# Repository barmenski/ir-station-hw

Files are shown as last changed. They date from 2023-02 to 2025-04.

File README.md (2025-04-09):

# Overview

IR rework station is made up of halogen lamp 250 mm for bottom heater, ceramic heater 450 Watts for top. Raspberry Pi B+ v1.2 controls the process.

## How to use

1. Install Raspbian on ypur Raspberry Pi https://www.raspberrypi.com/documentation/computers/getting-started.html#installing-the-operating-system
2. Install Node.js:
   1. Install NVM with the install script:
      `curl -o- https://raw.githubusercontent.com/nvm-sh/nvm/v0.40.1/install.sh | bash`
   2. Install the latest Long Term Support version of Node with NVM:
      `nvm install --lts`
3. Install Git:
   `sudo apt install git -y`
4. Clone repository:
   `git clone https://github.com/barmenski/ir-station-hw.git`
5. Go to ir-station-hw directory:
   `cd ./ir-station-hw/`
6. Install dependencies:
   `npm install`
7. Run:
   `node index.js`

## Peripheral devices connection diagram

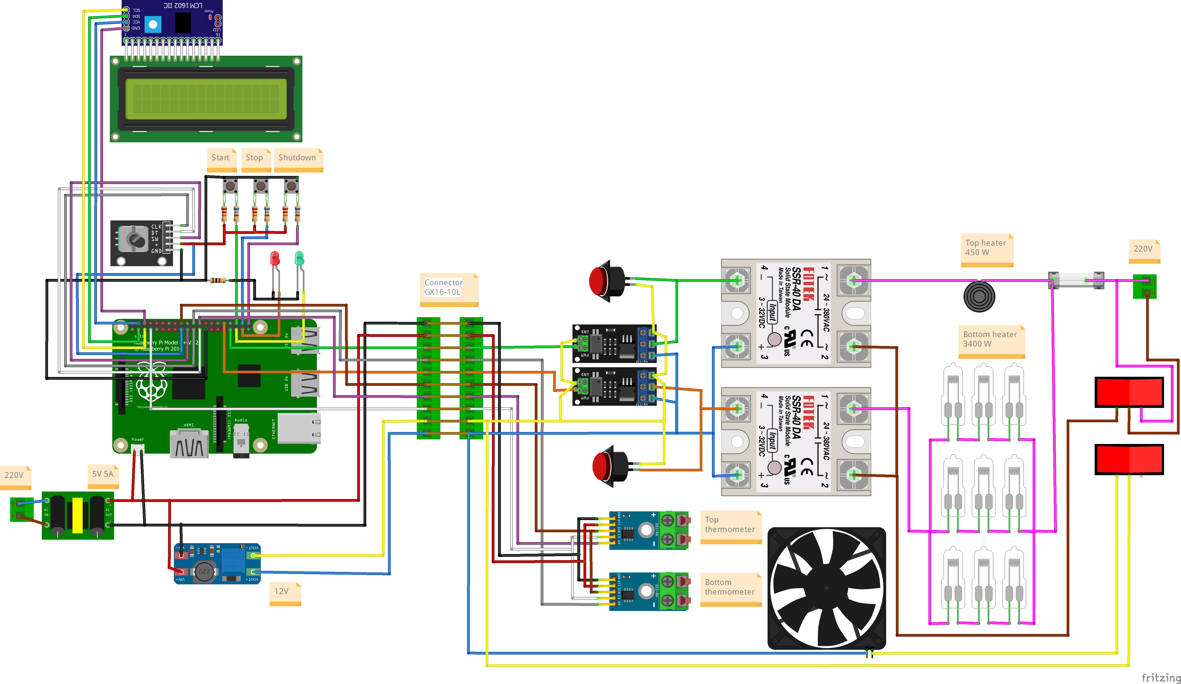
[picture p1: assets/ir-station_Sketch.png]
wiring


## Video of the device in operation

video1 (https://www.youtube.com/watch?v=XWZlBCWv8PI)

video2 (https://www.youtube.com/watch?v=XlxXhoq2SfA)

## How it works

- Raspberry Pi measures temperature using a module based on the MAX6675 chip and a K-type thermocouple.

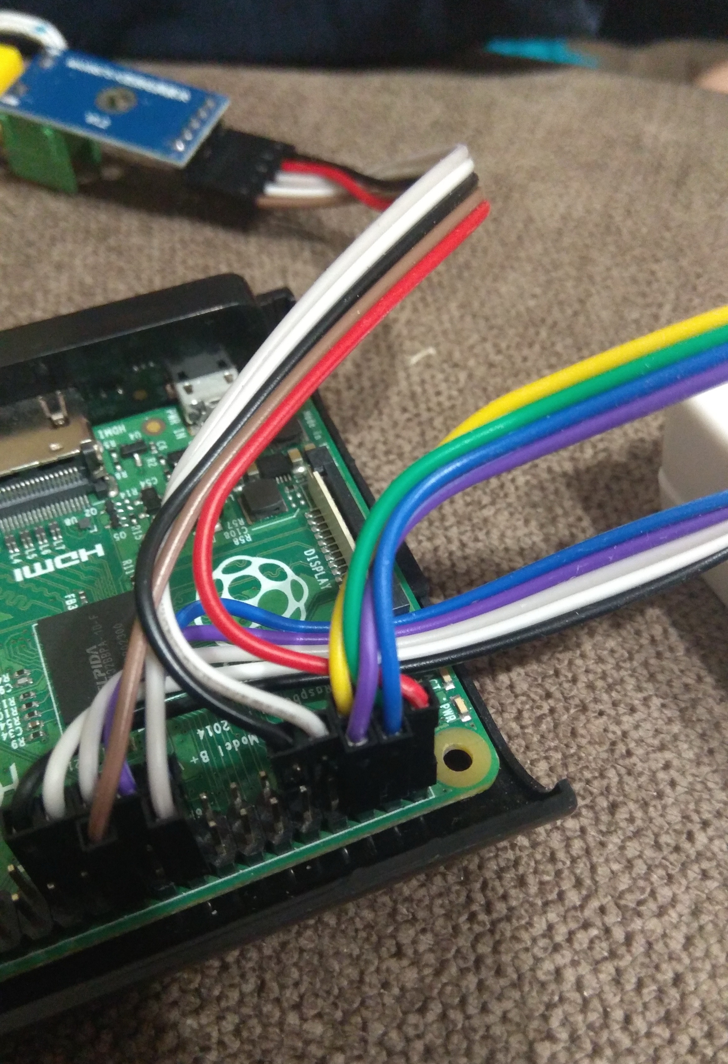
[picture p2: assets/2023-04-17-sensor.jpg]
measure


- Based on the measured temperature and the setpoint, the PID module calculates the percentage of power that must be supplied to the heaters.

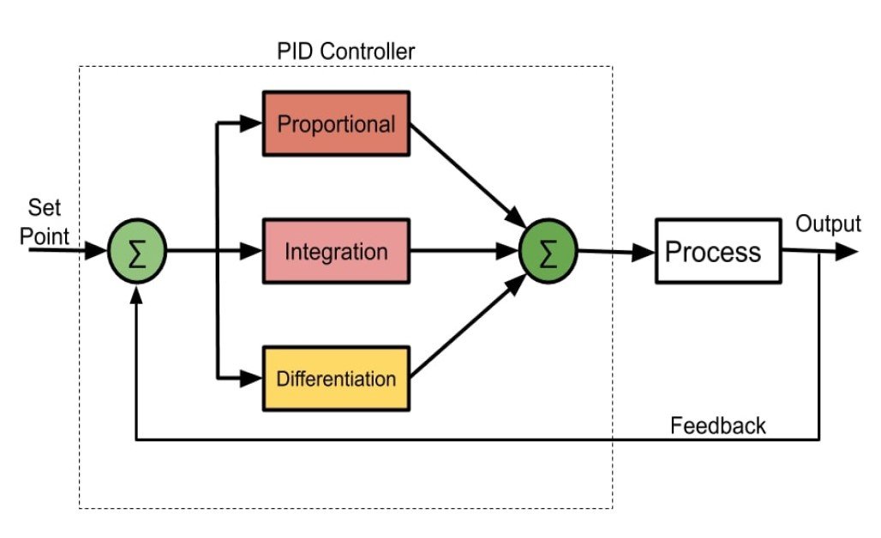
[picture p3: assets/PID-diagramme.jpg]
pid


- This percentage of power is transmitted to the PWM module, which controls the heaters.

pwm

- It is necessary to heat the chip at the required speed and for the required duration in order not to damage the chip with high temperature. These parameters are reflected in the thermal profile graphs. Thermal profiles differ for lead-containing solders (products before 2006) and lead-free solders:

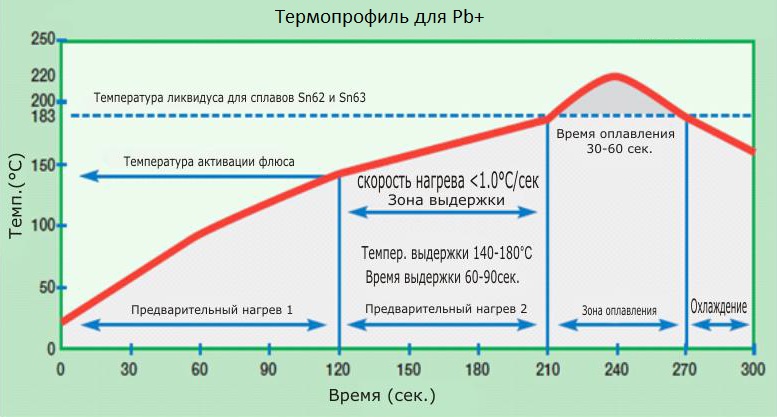
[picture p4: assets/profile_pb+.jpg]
pb+


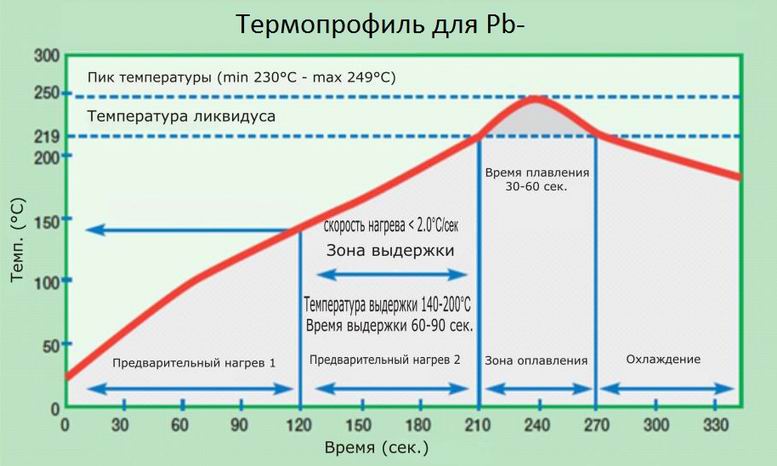
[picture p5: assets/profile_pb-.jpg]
pb-


- To heat according to the thermal profile, you need to select the item "Profil":

menu-profile

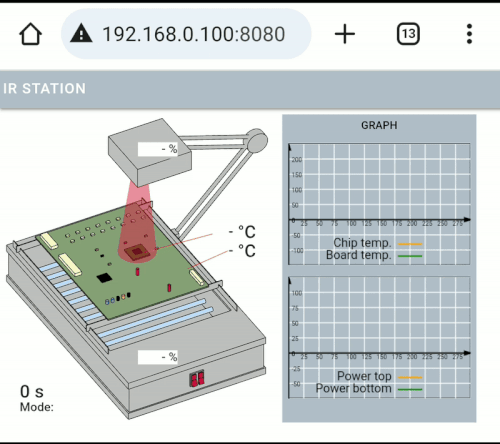
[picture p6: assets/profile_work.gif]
profile-work


- To heat and maintain the desired temperature, you must select the item "Const":

menu-const
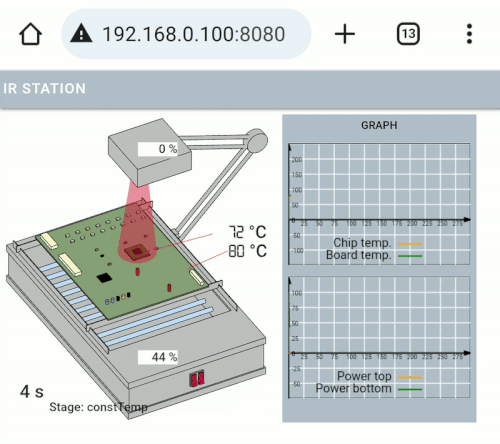
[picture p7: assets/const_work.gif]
const-work

const-video

- The application starts a simple server that receives data via `web-sockets` and draws graphs in `<canvas>`. The application connects to the network with its static IP 192.168.0.100:8080.

## TODO
- [ ] The ability to connect to a hotspot on phone

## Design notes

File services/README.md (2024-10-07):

# Make daemon of buttons handler
Copy /services/buttons_handler.service to /etc/systemd/system/buttons_handler.service

Edit daemon (for changing path, etc.):
`nano /etc/systemd/system/buttons_handler.service`
Make autolaunch for daemon:
`systemctl enable buttons_handler`
Start daemon now:
`systemctl start buttons_handler`
Status daemon (must be "running"):
`systemctl status buttons_handler`
Do similar actions with the file **ir_station.service**

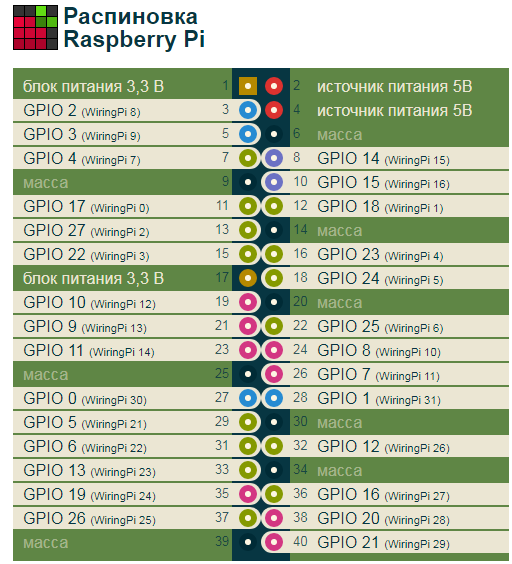
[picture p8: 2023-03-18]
assets/raspberrypi-pins-fr.png

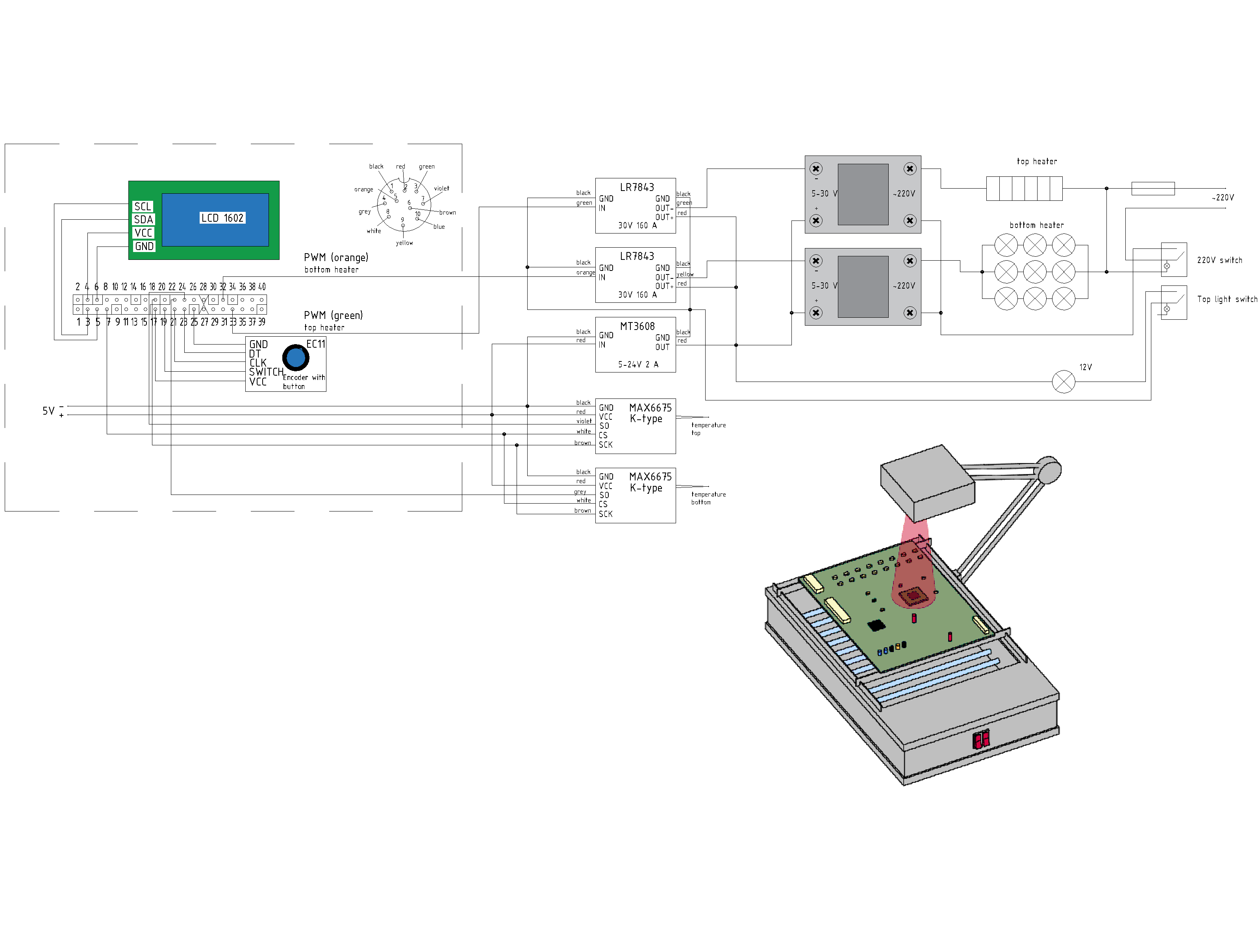
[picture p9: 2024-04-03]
assets/raspberrypi-pins.png

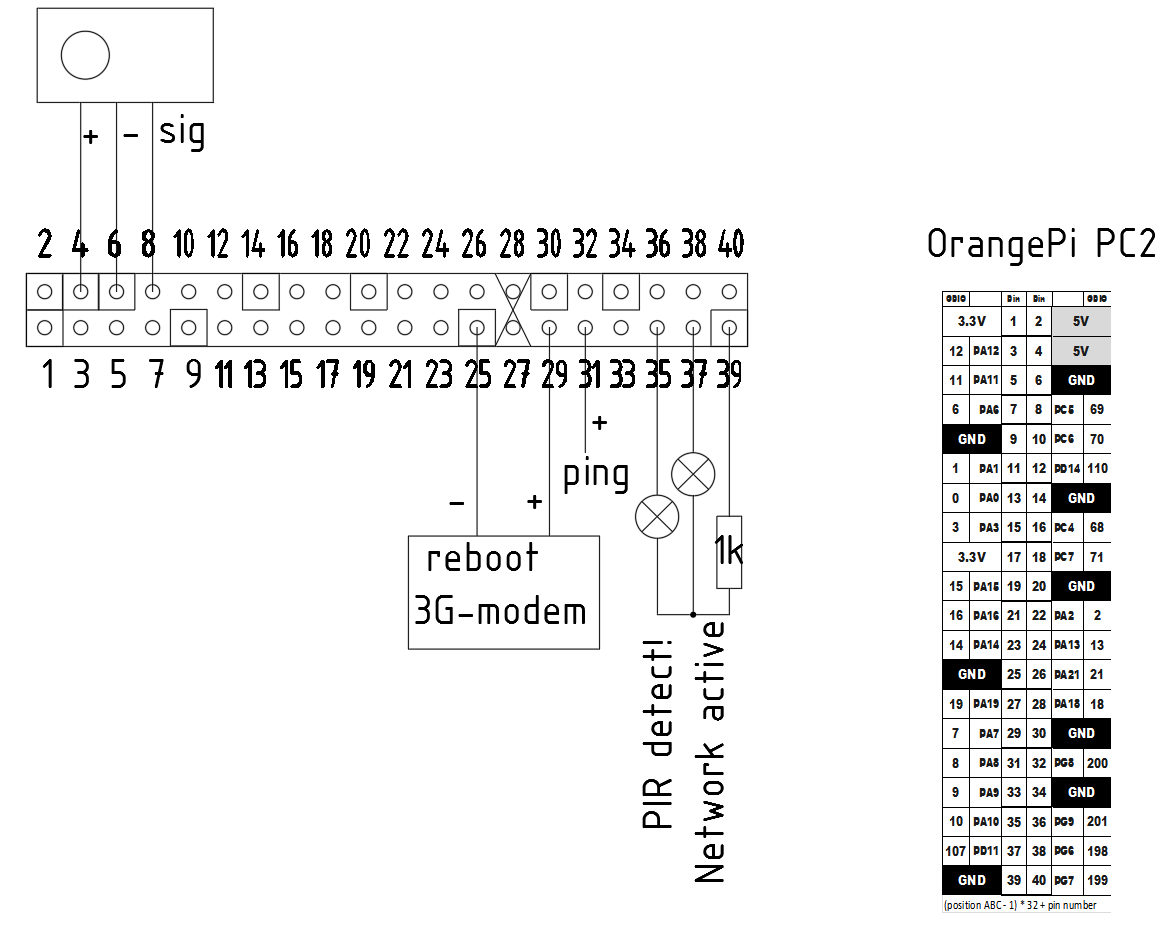
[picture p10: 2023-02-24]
assets/orangepi-pins.png

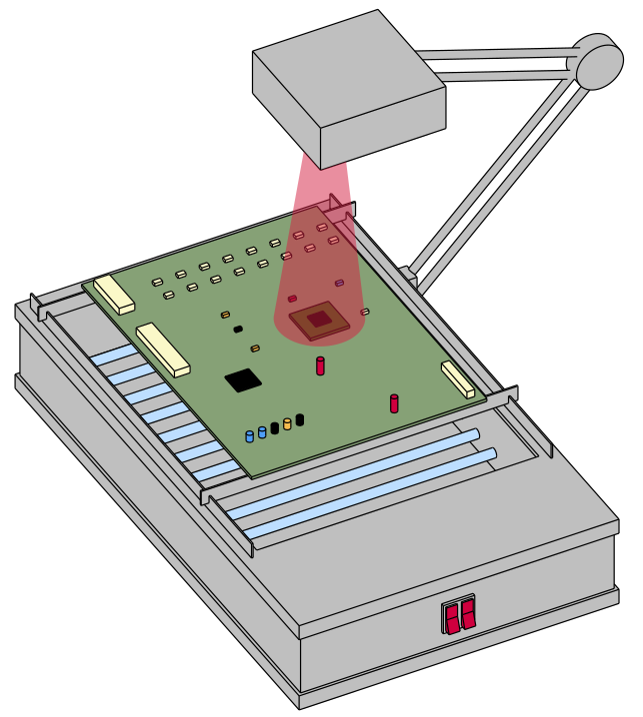
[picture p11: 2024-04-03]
assets/ir-station-model.png

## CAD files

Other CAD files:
assets/pins.dwg
components/src/assets/images/ir-station model flat.dwg
components/src/assets/images/ir-station model.dwg

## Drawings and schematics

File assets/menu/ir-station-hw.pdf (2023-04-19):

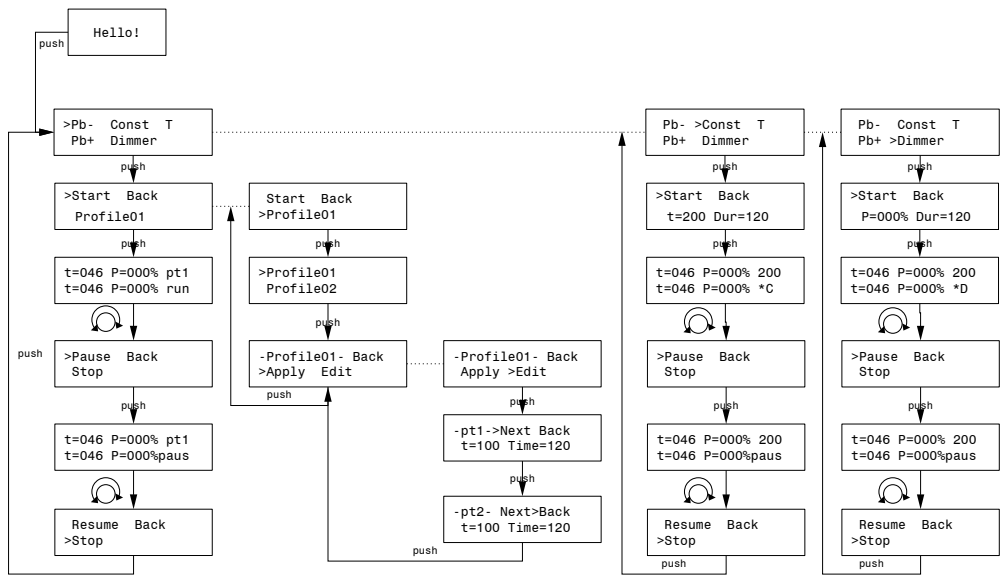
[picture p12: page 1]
Hello!; >Pb- Const T Pb+ Dimmer; push; >Start Back Profile01; t=046 P=000% pt1 t=046 P=000% run; >Pause Back Stop; t=046 P=000% pt1 t=046 P=000%paus; Start Back >Profile01; >Profile01 Profile02; -Profile01- Back >Apply Edit; -Profile01- Back Apply >Edit; Pb- >Const T Pb+ Dimmer; >Start Back t=200 Dur=120; Pb- Const T Pb+ >Dimmer; >Start Back P=000% Dur=120; -pt1->Next Back t=100 Time=120; -pt2- Next>Back t=100 Time=120; Resume Back >Stop; t=046 P=000% 200 t=046 P=000%paus

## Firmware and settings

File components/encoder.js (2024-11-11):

const rpio = require('rpio');
const EventEmitter = require('events');
const { POLL_LOW, POLL_HIGH } = require('rpio');
EventEmitter.defaultMaxListeners = 15;

class  Encoder extends EventEmitter {
	options = {
		gpiomem: false,
		mapping: 'physical',
		mock: undefined,
		close_on_exit: true
	  }
	pinS1 = 21;
	pinS2 = 23;
	pinKey = 19;
	i = 0
	constructor(){
		super();
		rpio.init(this.options);
		rpio.open(this.pinS1, rpio.INPUT, rpio.PULL_UP);
		rpio.open(this.pinS2, rpio.INPUT, rpio.PULL_UP);
		rpio.open(this.pinKey, rpio.INPUT, rpio.PULL_UP);
	}

	 #pollS1S2=() => {
		if (rpio.read(this.pinS1) == 1 && rpio.read(this.pinS2) == 1) {
			this.emit("rotate", -1);
			this.i--;
			rpio.msleep(1);
		  } else if (rpio.read(this.pinS1)==1 && rpio.read(this.pinS2)==0) {
			this.emit("rotate", 1);
			this.i++;
			rpio.msleep(1);
		  }
	}
	
	#pollKey=()=> {
		rpio.msleep(20);
		this.emit("pressed");
	}

	init=()=> {
		rpio.poll(this.pinS1, this.#pollS1S2);
		rpio.poll(this.pinKey, this.#pollKey, POLL_LOW);
	}

	stop=()=> {
		rpio.poll(this.pinS1, null);
		rpio.poll(this.pinKey, null);
	};
	


}
module.exports = Encoder;

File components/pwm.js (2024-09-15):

const rpio = require("rpio");

class PWM {
  pinTop = 33;// pwm1
  pinBottom = 32; // pwm0
  range = 100; /* Max PWM */
  clockdiv = 2048; /* Clock divider (PWM refresh rate), 8 == 2.4MHz 64=3khz 128=1.5khz 256=750hz*/

  constructor() {

  }

  init() {
    rpio.open(this.pinTop, rpio.PWM);
    rpio.open(this.pinBottom, rpio.PWM);
    rpio.pwmSetClockDivider(this.clockdiv);
    rpio.pwmSetRange(this.pinTop, this.range);
    rpio.pwmSetRange(this.pinBottom, this.range);
  }

  update(dutyCycle1, dutyCycle2) {
    rpio.pwmSetData(this.pinTop, dutyCycle1);
    rpio.pwmSetData(this.pinBottom, dutyCycle2);
  }

  stop(){
    rpio.open(this.pinTop, rpio.INPUT);
    rpio.open(this.pinBottom, rpio.INPUT);
  }
}

module.exports = PWM;

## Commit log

2023-02-23 add: image of pins
    [pins.dwg]
2023-02-23 make display temperature to 1602
2023-03-11 add: encoder
2023-03-18 add: some function for encoder
2023-03-18 edit: scheme of pins connections
    [pins.dwg]
2023-04-11 add: pid, menu files
2023-10-21 add: commited some missed things
    [pins.dwg]
2023-10-27 try temp measure
    [pins.dwg]
2024-02-22 fix: link constMenu→menu
2024-03-12 try rpio. stop feeling encoder rotate, press work
2024-03-12 pwm rpio test worked
    [pins.dwg]
2024-03-19 add: rpio packege, encoder work
2024-03-23 fix: encoder and pwm work on rpio
    [encoder.js]
2024-03-30 fix: pwm-signal see on 2 channel
    [encoder.js, pwm.js]
2024-04-03 update pins scheme
    [pins.dwg]
2024-06-12 add: buttons for control
2024-06-13 fix: dimmer change freq 97 hz
    [buttonsHandler.js, encoder.js, pwm.js]
2024-06-17 fix: encoder; add: led.js
    [encoder.js, led.js]
2024-06-24 fix: constTemp mode name of var
    [pidSet.json]
2024-06-27 add some pidMenu
    [pidSet.json]
2024-08-02 add: profil mode work with problems
    [led.js]
2024-08-04 fix: profile, delete pauseMenu, problem with time and speed heating
2024-08-18 fix: open index.html
    [ir-station model flat.dwg, ir-station model.dwg]
2024-08-31 fix: socket
2024-09-27 fix: profile heating by speed
2024-10-07 fix: buttons handler service
    [buttonsHandler.js]
2024-10-21 add: sMenu, add folder Menu
    [pidSet.json]
2024-10-31 fix: constTemp, led in dimmer
2024-11-10 add: set ip adress by encoder and lcd display
2024-11-30 fix: smenu change to simple show ip
    [ir-station Sketch.fzz]
2025-02-08 feat: add gap between stage2 stage3
    [1602.xlsx, ir-station Sketch.fzz, ir-station model flat.dwg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]
2025-02-08 fix: top heater stage 1 replace tempBoard to tempChip
2025-03-31 docs: readme edit
    [1602.xlsx]
